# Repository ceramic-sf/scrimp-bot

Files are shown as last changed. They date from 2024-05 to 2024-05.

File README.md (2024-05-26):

# scrimp-bot
Make a bot from what you've got

movements

Tier|Bot|Reason
|-|-|-|
|S||
|A||
|B|scrimp bot | +Functional +Frugal -Fragile -Fortissimo -Flawed|
|C||
|F||

## Contents

  - [Goal](#goal)
  - [Free hardware](#free-hardware)
  - [Rationale](#rationale)
  - [Roller screw technology](#roller-screw-technology)
  - [Parts list](#parts-list)
  - [Simple form](#simple-form)
  - [Scrimp friendly](#scrimp-friendly)
  - [How control works](#how-control-works)
  - [How the muscle works](#how-the-muscle-works)
  - [Gearing](#gearing)
  - [Muscle module force](#muscle-module-force)
  - [Arm torque](#arm-torque)
  - [Telescopic design](#telescopic-design)
  - [Stepper and driver](#stepper-and-driver)
  - [Findings](#findings)
  - [Improvements](#improvements)
  - [Brains](#brains)

## Goal

For about 100 USD, build an arm that can lift regular objects around in a regular working space.

## Free hardware

Scrimpbot is free and open hardware, please enjoy.

open hardware

## Rationale

Robotic foundation models will soon make smooth control of rickety robots trivial.

One must have a robot to try them out. Scrimp bot is made from cheap parts a 3D printing hobbyist may already have
(filament, stepper motors, M3 bolts).

Words in -> vision-movement 2Hz looping -> smooth task completion

By mounting webcams on the robot, a script that takes images at 2Hz can feed the images containing
the robot position and environment to a model. The model puts out instructions to send to the robot. This implies that fine control will be possible, even if
the robot is not ultraprecise. Humans cannot do things precisely with their eyes closed, and neither can scrimp bot.

Scrimp bot is manually controllable with a few potentiometers. That allows
some training data to be made. A model fine tuned on those episodes can later
be used instead of the manual controller.

```mermaid
quadrantChart
    title Different Robots
    x-axis Basic Robot --> Complex Robot
    y-axis Basic Control --> Complex Control
    quadrant-1 Robust / SOTA / Future
    quadrant-2 Accessible and useful
    quadrant-3 Novelty
    quadrant-4 Manufacturing / Academia
    Octo + stepper: [0.1, 0.6]
    Octo + 3D printed arm: [0.25, 0.65]
    Optimus: [0.65, 0.75]
    Atlas: [0.85, 0.40]
    Spot: [0.60, 0.55]
    Arduino + 3D printed arm: [0.25, 0.25]
    Kuka: [0.55, 0.25]
```

## Roller screw technology

The main moving part in scrimpbot is the inverted planetary roller screw.

Its just a screw, but with low friction. That's good for robotics because
you don't want to lose any energy. Screws are nice because they can push heavy loads and you can tune them to make them stronger or faster.

If you want to explore this mechanism, consider printing this vise I designed and having a play. The roller screw there is the same that is used in scrimp bot.

[https://github.com/ceramic-sf/vice-vise/tree/main](https://github.com/ceramic-sf/vice-vise/tree/main)

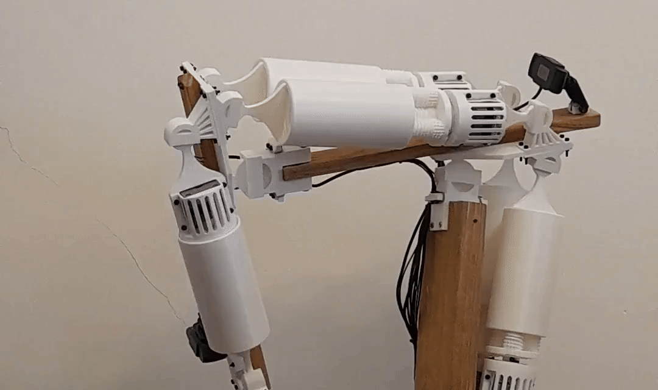
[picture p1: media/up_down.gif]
up_down


## Parts list

One may have most of these around the house.

| Item | Units | USD/unit | USD total | Mass/Unit (g) | Mass total (g) |
|---|---|---|---|---|---|
| PLA 1kg | 2 | 25 | 50 | 1000 | 2000 |
| NEMA 17 stepper motor | 5 | 5 | 25 | 300 | 1500 |
| M3 bolts/nuts 300pcs | 2 | 8 | 16 | 100 | 200 |
| Webcam 340p | 3 | 5 | 15 | 30 | 90 |
| TMC2208 drivers | 5 | 2 | 10 | 5 | 25 |
| Super glue tube | 3 | 2 | 6 | 1 | 3 |
| Wire 1m | 10 | 0.5 | 5 | 10 | 100 |
| Wood 2x4 1m | 1 | 5 | 5 | 1500 | 1500 |
| Variable resistors | 5 | 1 | 5 | 3 | 15 |
| Arduino | 1 | 5 | 5 | 25 | 25 |
| Power supply 24V 5A | 1 | 5 | 5 | 200 | 200 |
| Electrolytic Capacitor 100uF  | 1 | 1 | 1 | 1 | 1 |
| Rubber bands | 10 | 0.1 | 1 | 0.1 | 1 |
| **TOTALS** | | | **170** | | **5660** |

## Simple form

A mechanical muscle module that can lengthen and contract. Make multiple muscles to "flesh out" a robot skeleton.

The skeleton is wooden with some ball and socket joints.
Two muscles acting together can make a single joint roll, pitch and yaw. Multiple
joints allows for a large range of motion, similar to that of a human arm.

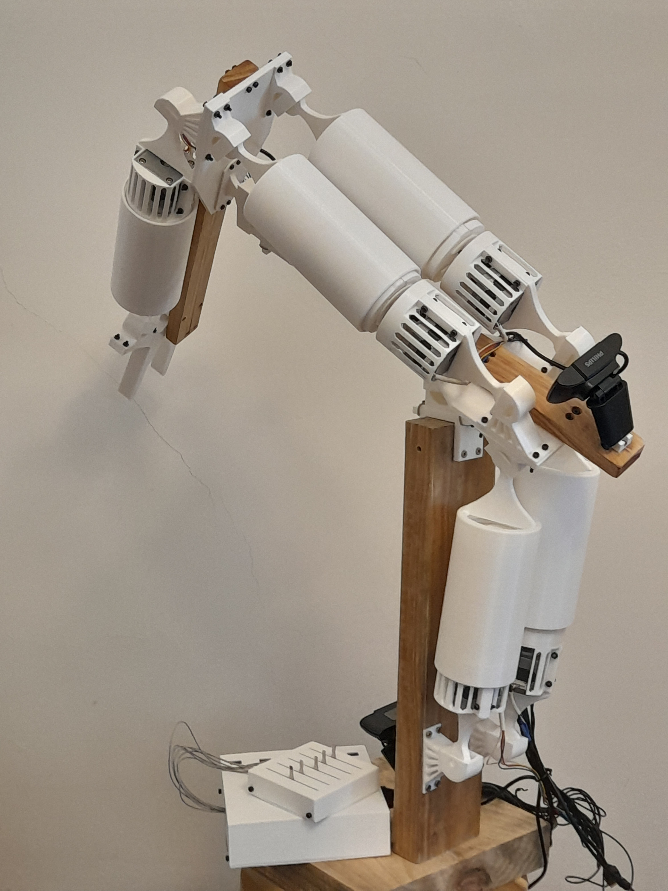
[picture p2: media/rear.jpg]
rear


## Scrimp friendly

The muscle module can fit any stepper size and length you have. The
FreeCAD model uses paramater based design and updating stepper sizes in the
CAD spreadsheet updates the physical model.

To use the FreeCAD model, open the `./models/muscle_motor_assembly.FCStd` file. The Assembly4 workbench is used to bring together different parts.

## How control works

Electronics go in a 3D printed box with some sliders that act as a remote control.

The human looks at the arm and moves the resistors, one per muscle.
Each resistor is read by the arduino and converts position into a velocity.
The signal is sent to the stepper driver, which sends signals to the stepper. The stepper spins
the roller screw, which changes the muscle length. The arm moves. One muscle operates a crab claw.

Theoretically, the control box can be removed and the webcams turned on. Then
one would type instructions on a laptop, and a robot foundation model would move scrimbot

## How the muscle works

Stepper motors are high torque with low speed. A 34mm NEMA17 can get about 3 rotations per second
(180RPM). If applied to a screw system with a lead of 5-15mm/rotation that can result in a linear movement of
15-45mm/sec. This linear movement is the same as the linear movement of a contractile muscle, simply fix it to a bone either side of a joint.

## Gearing

A roller screw is useful in transmitting work efficiently (80-90%). The screw can be designed
to have higher speed or higher torque. This allows the mechanical advantage to be tuned
easily.

For a better understanding of how this works, try out this
[roller screw recipe](https://github.com/ceramic-sf/vice-vise/blob/main/roller_screw_recipe.md).

Additionally, the where the muscle is attached and how long the limb is can be modified
for higher speed or higher torque.

## Muscle module force

The stepper motor performs work during a full revolution. That work
is equal to the work done by the muscle module which exterts a constant force
over the lead of the roller screw.

Let's calculate the force. We know what torque the stepper exerts (datasheet). We
know that the force exterted will be different if the lead is high (low torque) or
low (high torque).

Mechanically this is the same as a rack (screw) and pinion (stepper). The pinion
gear turns one revolution and the rack moves one lead distance. So the pinion circumference is equal to the screw lead. That lets us calculate the radius of the
pinion, which is where the force is being exterted on the rack.
```
stepper_torque_nm = force_exterted_n * pinion_radius_meters
force_exerted_n = stepper_torque_nm / pinion_radius_meters
```
Where:
```
circumference_pinion_meters = roller_screw_lead_meters
```
Replace circumference with radius and rearrange:
```
pinion_radius_meters = roller_screw_lead_meters / 2 * pi
```
So, the newtown force for a given newton meter torque input of a stepper motor
driven roller screw is:
```
force_exerted_n = 2 * pi * stepper_torque_nm / roller_screw_lead_meters
```

Leads are usually in millimeters and stepper datasheets often have kgcm torque. Where:
```
stepper_torque_nm = stepper_torque_kgcm * g_gravity / 100
```
The useful formula is:

```
force_exerted_n = 20 * pi * g_gravity * stepper_torque_kgcm / roller_screw_lead_millieters
```
Simplified:
```
force_exerted_n ~= 630 * stepper_torque_kgcm  / roller_screw_lead_millimeters
```
However, transmission of a roller screw is not perfect (80-90% efficient).
Using 80% efficiency:
```
force_exerted_real_n = 500 * stepper_torque_kgcm / roller_screw_lead_millimeters
```
Which for a cheap step stepper with 1.3kgcm torque and a lead of 10mm results
in a torque of ~65N.

## Arm torque

The stepper motor has torque that drives the screw, which exterts a constant push or pull force. That force is applied on the moving bone of a skeleton, some distance from the joint.

We can attach the muscle module to work as a first-class (seesaw, tricep muscle) or a second-class  (wheelbarrow, bicep muscle) lever. A first class keeps the
muscles more out of the way.

So the muscle attaches on one side of the joint (`attached_distance_m`) and
moves the arm (`arm_length_m`).

The largest mass that can be lifted by an arm with a single muscle motor module can be calculated. Let the muscle torque and the lifting torque be equal:

```
muscle_module_force * attached_distance_m = kg_liftable * g_gravity * arm_length_m
```
So max `kg_liftable`:
```
kg_liftable = muscle_module_force * attached_distance_m / (g_gravity * arm_length_m)
```

We now use the muscle module force calculation from before:
```
kg_liftable = 50 * stepper_torque_kgcm * attached_distance_m / (arm_length_m * roller_screw_lead_millimeters)
```

So if we use a standard NEMA17, a 10mm lead, connect the muscle 10cm from the joint and have the arm be 40cm long then the liftable mass is 1.6kg.

The actual prototype has a 4mm lead, muscle connected at 10cm, and a 30cm arm. So the liftable mass is 5.4kg. Two muscles are used, which gives ~10kg liftable mass in theory. Some of that mass will be lifting the outer parts of the arm (wrist and claw motors and parts).

## Telescopic design

In this design, the stepper motor is integrated with the inverted planetary roller screw to form a plug and play
motor muscle module.

The main features of this design are:
- The stepper motor is protected from axial loads via a printed slew bearing
- The stepper motor telescopes into the nut of the roller screw which reduces the length of the
muscle module.

An inverted planetary roller screw facilitates the teslescope action, where a non-inverted
would not.

## Stepper and driver

Old discarded NEMA17 steppers:
- Model: KH42HM2B017
- Coil: 30ohms/phase
- Current: 0.82A/phase
- Rated holding torque: 1.3kgcm
- Axial housing length: 34mm

Driver:
- Model: TMC2208 (the stepper is nearly silent with this driver)
- Mode: Half step (reduces torque, but full step requires sending driver signals in a more complicated way)
- Current limit: 0.54A
    - `reference_voltage = max_current * 1.41 = 1.0V`
    - Initially 0.8A was used (stepper datasheet), but was too hot.

See [scrimp_bot_wiring.md](./scrimp_bot_wiring.md) for a wiring diagram of all connections for electronics.

## Findings

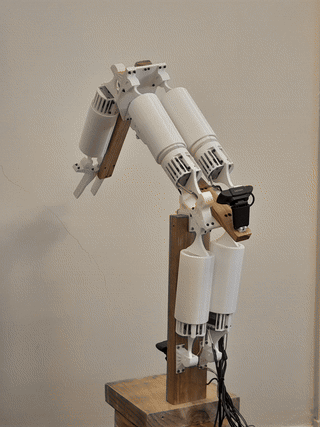
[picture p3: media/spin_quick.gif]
spin


It works, but some mods are in order.

| Feature | Problem | Suggestion |
|---|---|---|
|Muscle modules|Large diameter means they rub|Stop telescoping stepper into nut.|
| Stepper Motor Telescoping | Stepper motor makes the nut large and modules rub | Place stepper next to nut and drive the nut |
| Stepper Motor Telescoping | Roller screw cannot be sealed for noise and lubrication | Keep stepper out of nut, seal mechanism |
| Thread Starts | One thread start makes the screw structurally vulnerable. | Use 2 or 3 thread starts to improve structural integrity. |
| Motors always on | Motors reach around 70 degrees, causing PLA to glass. | Turn off current when not moving. |
| Bearings | Bearings add friction and may be unnecessary as PLA would break first. | Remove bearings and let stepper take axial load. |
| Stepper Motor Installation | Stepper motor is fiddly to install. | Use a face plate for easier installation and removal. |
| Stepper Motor Shaft | No grip for the grub screw. | Grind the shaft to a "D" shape for better grub screw grip. |
| Lift Capacity and Speed | Lift capacity is good, but movement is slow. | Use longer stepper motors and higher lead roller screws. |
| Ball and Socket Joints | Joints work well but had a dislocation. | Reinforce socket or redesign joints. |
| Tendon-Based Attachments | Tendon-based attachments need supports to print | Separate tendons fromo joints |
| Stepper Motor Enclosure | Enclosure obstructs heat dissipation, potentially causing PLA to melt. | Design the enclosure to improve heat dissipation. |
| Noise Level | Mechanism is moderately noisy. | Seal and lubricate the mechanism to reduce noise. |

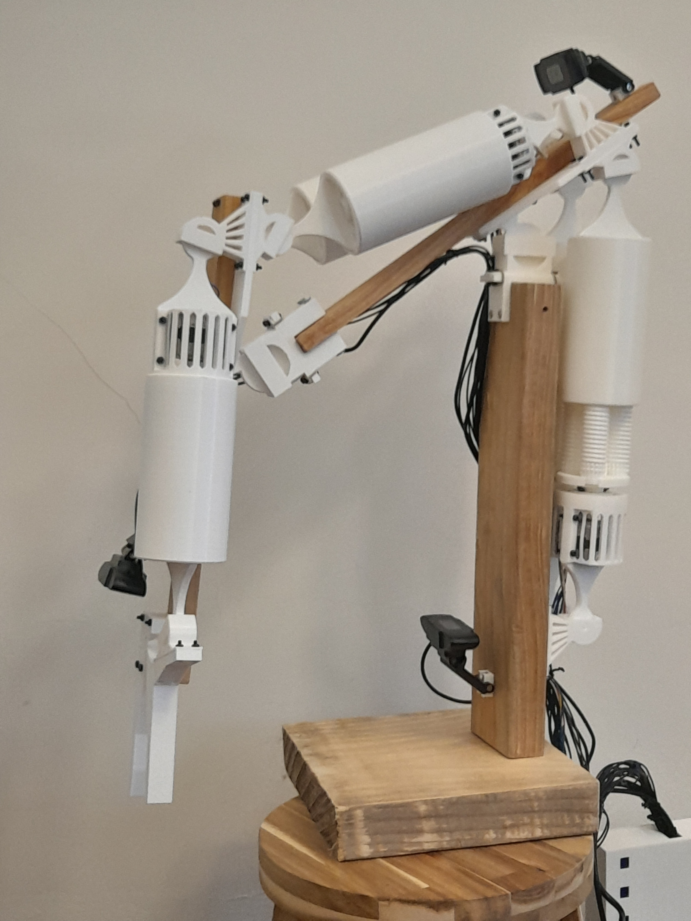
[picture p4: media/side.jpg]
side


## Improvements

A next iteration of scrimp bot given the above findings Given the above direction is:
- Reduce complexity
- Remove features

New design:
- Stepper bolted to a hinge
- Stepper shaft bolted to end of nut
- Muscle motor modules will have smaller radius
- Roller screw mechanism stays inside nut
- A cental screw extension rod is bolted to a joint

## Brains

Scrimpbot can theoretically be driven by a robotic foundation model.

See [scrimp bot brains](./scrimp_bot_brains.md) for a work-in-progress walkthrough of the most straightforward path I can see being feasible.

The hardware roughly looks like this:
```mermaid
---
title: Hardware arrangement
---
flowchart LR
    subgraph computer[server]
        octo[octo weights]
        subgraph scripts[python scripts]
            photo[take photos] --> inference
            inference[run octo inference] --> command
            command[send motor commands]
        end
        camera[webcam]
    end

    subgraph robot
        driver[stepper driver]
        command --> driver
        power[power supply] --> capacitor
        capacitor --> driver
        driver --> motor
    end
```

The software mainly does this:
```mermaid
---
title: Cycle repeated every n milliseconds
---
flowchart TD
    camera[camera takes photo of robot] --> inference[octo inference run on photo to get rotation commands]
    inference --> commands[rotation step commands to driver]
    commands --> driver[driver converts steps to electric pulses] --> motor[motor moves to some new position]
    motor --> camera
```

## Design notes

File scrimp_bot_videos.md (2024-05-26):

Scrimp bot is noisy, see [./media/raw_with_audio.mp4](./media/raw_with_audio.mp4)
for a sample with audio. The roller screws are open and resonate inside the large PLA nut cylinder.

When you extend a muscle too far, nothing stops it from falling apart.

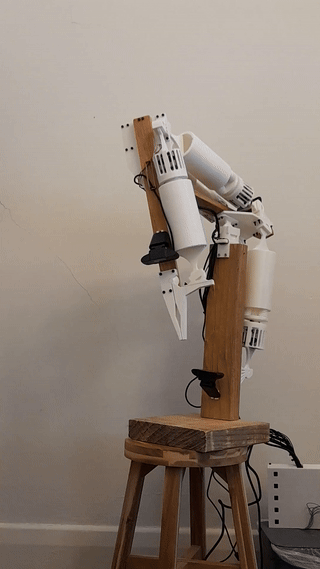
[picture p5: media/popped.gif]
popped


Demo of how the joints tilt.

side_to_side

Range low down.

sweep

Preparing the claw to grab something.

go_to_grab

Scrimp bot is hard to get where you want exactly.

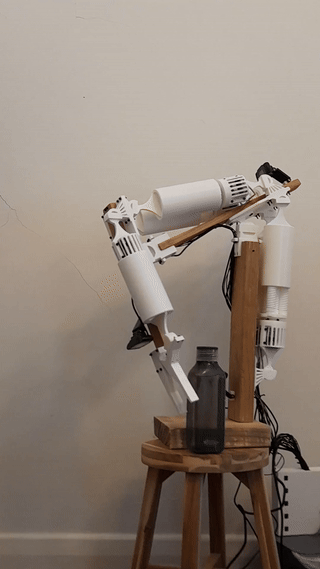
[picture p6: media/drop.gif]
drop


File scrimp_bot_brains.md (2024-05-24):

# scrimp bot box

How to use Engligh sentences to control a home made robot.

"Grab to the banana"

Status: Ideas/research phase.

Progress: Search for the "🚧 progress marker 🚧" below.

## Introduction

An exploration of the Octo robot control model ([https://github.com/octo-models/octo](https://github.com/octo-models/octo)) running on a dedicated box connected to a cheap
homemade robot.

Octo uses images of the robot to work out what the robot should do. Cheap webcams are attached
to the robot, the cameras can see part of the robot and part of the environment.
Cameras are the only positional feedback that the robot has.

## Server setup

An i5 without is used without a dedicated GPU. Webcams and arduino are
plugged in over USB.

- Download ubuntu, burn to usb, install on pc, configure, SSH in from laptop

## Robot hardware setup

Build a robot that can be controlled by an arduino.

- Construct parts, add motors, connect drivers to motors, connect arduino to drivers.

## Robot software setup

Create a python script that can send data to the arduino via serial interface.

## Using octo to move the robot

Scrimp bot is a single stepper motor in front of a camera that can point
to objects drawn on a clockface. It is controlled by text input to a vision-enabled transformer that outputs
rotation commands.

scrimp bot is interesting because you can keep adding motors and
sensors and make incremental progress to more accessible and useful
robotics.

```mermaid
quadrantChart
    title Different Robots
    x-axis Basic Robot --> Complex Robot
    y-axis Basic Control --> Complex Control
    quadrant-1 Robust / SOTA / Future
    quadrant-2 Accessible and useful
    quadrant-3 Novelty
    quadrant-4 Manufacturing / Academia
    Octo + stepper: [0.1, 0.6]
    Octo + 3D printed arm: [0.25, 0.65]
    Optimus: [0.65, 0.75]
    Atlas: [0.85, 0.40]
    Spot: [0.60, 0.55]
    Arduino + 3D printed arm: [0.25, 0.25]
    Kuka: [0.55, 0.25]
```
Octo accepts language commands and sensor input and outputs commands for a robot controller to follow.

This is interesting because you can give a complicated command like "point to the cat"
and the model will watch as progress unfolds and update commands on the fly.

One can imagine a robot with only cameras for sensors and direct motor control. This walkthrough
attempts that with a single stepper motor with a camera pointed at it. The motor can rotate to
point at different pictures. An instruction "point to the cat" can be given, the model
is regularly fed camera frames of the motor, the model outputs rotation commands, and the commands
are sent by a microcontroller to the motor.

First we will try with the model as it is published, which would be an environment the model
has never seen and may not work well. Then we can fine tune the model by recording episodes
manually and then storing them in a particular format and fine tuning the model.

If the basic test works, it will be easy to add more motors and cameras. At that point we would
have a robot arm that only relies on sight for control, and it would be good to see if complex and
precise tasks could be performed. From there, one could make a two handed robot and see if that
works. Sensors can also be added as inputs. At this point, one could have a low cost
robot arm setup that can respond to human language.

### Observations
We can see that the model will accept a primary image and/or a wrist image.
We have only passed a primary image (supposed to be a main image of the robot,
but we used a dummy image).

These are all things that we can redefine when fine tuning the model later.
So a robot may have 3 images from different angles, and no wrist image. Or
it may have only one image and several force sensors.
```console
Observations: {
    image_primary: ('batch', 'history_window', 256, 256, 3),
    image_wrist: ('batch', 'history_window', 128, 128, 3),
}
```
### Tasks
We sent a text task, but we could have also sent a target image. That
is, an ideal end point that the robot should look like once it is finished,
either from zoomed out, or from the wrist perspective.
```console
Tasks: {
    image_primary: ('batch', 256, 256, 3),
    image_wrist: ('batch', 128, 128, 3),
    language_instruction: {
        attention_mask: ('batch', 16),
        input_ids: ('batch', 16),
    },
}
```
### Actions
Then we see actions the model thinks are appropriate.

The model produces 7 actions, 4 steps into the future. We can that there are
4 sets of seven action values in the output:
```console

'pick up the fork' actions:
[[[ 0.69299155  0.19062363 -0.05662455  0.18763681  0.07296022
   -0.3521931   1.0031093 ]
  [ 0.9940647   0.23903748 -0.11212341  0.32031953 -0.00594463
   -0.4033823   0.9950697 ]
  [ 1.130245    0.18083405 -0.37783027 -0.36048374  0.25762615
   -0.5909108   0.9917318 ]
  [ 0.7212891  -0.0667934  -0.48938182 -0.23768651 -0.03046823
    0.13813896  0.9990556 ]]]

'push the apple' actions:
[[[ 0.88822544  0.03327435 -0.01053857  0.11183605  0.22582716
   -0.25007552  1.0030512 ]
  [ 1.2086031   0.0545348  -0.17068534  0.21365923  0.18337864
   -0.3036416   1.0020596 ]
  [ 1.2331996  -0.00789991 -0.5044224  -0.3035693   0.39421743
   -0.44048995  0.9858144 ]
  [ 0.838152   -0.22254696 -0.6525285  -0.26379094 -0.10052849
    0.11552006  1.0055982 ]]]
```
So the model thinks that the first thing we should instruct the
robot to do to pick up the fork is:
```json
[ 0.69299155  0.19062363 -0.05662455  0.18763681  0.07296022 -0.3521931   1.0031093 ]
```
What do these values mean? Each robot will have different ways to control it.
So `0.692` could mean:
- Move motor one `0.69` meters
- Move motor two `69%` of a full rotation
- Close gripper until `0.69N` of force is archieved.
- ...

We will need to think about what actions are appropriate for our robot,
then define them in the model. The model will then be able to output
actions that can be used. If the robot is different from anything it has
seen, or the robot control problem is very difficult, then fine tuning
on examples will be required to allow the model to learn. After
learning, the model will be better at selecting actions that achieve
the tasks better.

## Looping

Take photo, run model, send action to robot, repeat.

A single inference took 0.18s to run on a quad core i7. This implies
that you could complete 5 send command, receive image cycles per second.

## Changing the model output

Octo accepts two images (primary, wrist) and outputs seven values.

```mermaid
---
title: Off the shelf Octo configuration
---
flowchart TD
    subgraph observations
        primary[primary image]
        wrist[wrist image]
    end
    observations --> octo --> actions
    subgraph actions
        floats[7 numbers]
    end
```
Additionally, the model is configured to use previous images and predict future
actions as follows
- `history_window`. How many previous inputs to use, default is 2.
- `action_chunking`. How many actions to predict, default is 4.

```mermaid
---
title: historical window size and action chunking
---
flowchart TD
    subgraph history[history windows, `window_size=2`]
        obs_m_1[observation m - 1]
        obs_m[observation m]
    end

    octo
    obs_m_1 & obs_m --> octo

    subgraph action[action chunking, 'pred_horizon=4']

        act_n[action n]
        act_n_1[action n + 1]
        act_n_2[action n + 2]
        act_n_3[action n + 3]
    end
    octo --> act_n & act_n_1 & act_n_2 & act_n_3
```

The model is defined here `./octo-small/config.json`, and the key parts
of the config are:
- `model`
    - `observation_tokenizers`
        - `primary` (image)
        - `wrist` (image)
    - `task_tokenizers` (text input)
    - `heads`
        - `action`
            - `action_dim` (size of each model action)
            - `pred_horizon` (number of actions to output per inference)
    - `window_size` (number of historical positions to use)

### Understanding model modifications
The octo repo example `./octo/examples/02_finetune_new_observation_action.py` shows how to modify the model to be used in the Aloha dataset. This is a bimanual robot.
We will use that to learn how changing the observations and actions of
a model works.

```mermaid
---
title: (Example 2) Aloha fine tuning example Octo configuration
---
flowchart TD
    subgraph observations
        primary[primary image]
        proprioception[14 proprioception numbers]
    end
    observations --> octo --> actions
    subgraph actions
    floats[14 numbers]
    end
```
Interestingly, the Aloha example does not use multiple historical windows.
```mermaid
---
title: (Example 2) Aloha historical window size and action chunking
---
flowchart TD
    subgraph history[history windows, `window_size=1`]
        obs_m[observation m]
    end

    octo
    obs_m --> octo

    subgraph action[action chunking, 'pred_horizon=50']

        act_n[action n]
        act_n_1[action n + 1]
        act_n_2[action ...]
        act_n_3[action n + 49]
    end
    octo --> act_n & act_n_1 & act_n_2 & act_n_3
```

First, the `./octo-small/config.json` config is read. Then it is modified
to suit the Aloha dataset.

```python
# `./octo/examples/02_finetune_new_observation_action.py`
def main(_):
    # ... (omitted)
    # Load octo-small config
    pretrained_model = OctoModel.load_pretrained(FLAGS.pretrained_path)
    # Load new dataset
    logging.info("Loading finetuning dataset...")
    dataset = make_single_dataset(
        dataset_kwargs=dict(
            name="aloha_sim_cube_scripted_dataset",
            data_dir=FLAGS.data_dir,
            # One input image.
            # This is a helper as images are labelled "top", not "primary"
            image_obs_keys={"primary": "top"},
            # In the dataset, proprioception is called "state" and has 14 elements.
            state_obs_keys=["state"],
            language_key="language_instruction",
            action_proprio_normalization_type=NormalizationType.NORMAL,
            # An action contains 14 values.
            absolute_action_mask=[True] * 14,
        ),
        traj_transform_kwargs=dict(
            # No historical windows.
            window_size=1,
            # Produces the next 50 actions every inference (action chunking).
            future_action_window_size=49,
        ),
        frame_transform_kwargs=dict(
            resize_size={"primary": (256, 256)},
        ),
        train=True,
    )
    # ... (omitted)

    config = pretrained_model.config
    ### The wrist camera observation is not needed for Aloha.
    del config["model"]["observation_tokenizers"]["wrist"]

    ### Add new observation for proprioception ()
    config["model"]["observation_tokenizers"]["proprio"] = ModuleSpec.create(
        LowdimObsTokenizer,
        n_bins=256,
        bin_type="normal",
        low=-2.0,
        high=2.0,
        obs_keys=["proprio"],
    )
    # Fully override the old action head with a new one (for smaller changes, you can use update_module_config)
    config["model"]["heads"]["action"] = ModuleSpec.create(
        L1ActionHead,
        pred_horizon=50,
        action_dim=14,
        readout_key="readout_action",
    )
```
We can use this code to understand how to change the model to suit a new robot.

### Define the scrimp bot model

We would like to make it accept one image (camera view of the motor) and output two values (a rotation command to motor and a "finished" signal). We will keep the window size and prediction horizon as the default values until there is a good reason to change them.

```mermaid
---
title: Desired basic Octo configuration
---
flowchart TD
    subgraph observations
        primary[primary image]
    end
    observations --> octo --> actions
    subgraph actions
    floats[2 numbers]
    end
```
So, we could follow a similar procedure for a new model definition and dataset.
We can do that later. We will first test the unaltered model to understand the
control system.

## Hardware

For using the octo model to control the robot:

- Server
    - Intel i5
    - 16Gb RAM
    - 100GB drive
- MicroSD with >4GB
- 3x cheap USB webcams
- Stepper motor driver (e.g., A4988 or TMC2208)
    - More info see here https://howtomechatronics.com/tutorials/arduino/stepper-motors-and-arduino-the-ultimate-guide/
- NEMA17 stepper motors
- 24V AC to DC converter rated to 1A or more
- 100uF electrolytic capacitor

```mermaid
---
title: Hardware arrangement
---
flowchart LR
    subgraph computer[server]
        octo[octo weights]
        subgraph scripts[python scripts]
            photo[take photos] --> inference
            inference[run octo inference] --> command
            command[send motor commands]
        end
        camera[webcam]
    end

    subgraph robot
        driver[stepper driver]
        command --> driver
        power[power supply] --> capacitor
        capacitor --> driver
        driver --> motor
    end
```

```mermaid
---
title: Cycle repeated every n milliseconds
---
flowchart TD
    camera[camera takes photo of robot] --> inference[octo inference run on photo to get rotation commands]
    inference --> commands[rotation step commands to driver]
    commands --> driver[driver converts steps to electric pulses] --> motor[motor moves to some new position]
    motor --> camera
```

### Later: Hardware for fine tuning

For fine tuning the octo model

- Server and robot setup from before
- Manual control system to move the robot.
    - For a single-motor robot, a resistor pot and a script to control stepper motor velocity
    is enough
    - Keyboard input mapped to each joint
    - For a complex robot, a miniature robot rigged with resistor pots can be used to control the
    large one naturally
    - Joystick configured to control end effector movements
- GPU
    - NVIDIA GPU with at least ~1GB VRAM
- Time to perform robot movements manually and record data for ~50 episodes "things you want the
robot to do"
- Time to run fine tuning

## Set up dedicated server

Flash the SD card with ubuntu server.
SSH in.

```
ssh scrimpbot@<serveripaddress>
sudo apt update && sudo apt full-upgrade
sudo apt install -y python3-pip make build-essential libssl-dev zlib1g-dev \
libbz2-dev libreadline-dev libsqlite3-dev wget curl llvm libncurses5-dev \
libncursesw5-dev xz-utils tk-dev libffi-dev liblzma-dev git-lfs
```
Install pyenv as per https://github.com/pyenv/pyenv

Make an environment
```
mkdir scrimpbot && cd scrimpbot
pyenv install 3.10
pyenv virtualenv 3.10 scrimpbot-venv
pyenv activate scrimpbot-venv
```

Get octo and install octo as a python package
```
git clone https://github.com/octo-models/octo.git
```
In `requirements.txt`, make sure that scipy is `scipy>1.6.0,<=1.12.0` (see https://github.com/octo-models/octo/issues/71).
```
pip install -e octo
pip install -r octo/requirements.txt
pip install --upgrade "jax[cpu]==0.4.20" jaxlib
```

Download the small octo model (27M params)
```
git clone https://huggingface.co/rail-berkeley/octo-small
```
See that the ~500MB of weights are installed (requires git lfs)
```
du -sh octo-small/270000
> 522M	octo-small/270000
```
Create a test script
```
cd /home/scrimpbot/scripts
nano basic_inference_test.py
```
Containing:

```py
import jax
from octo.model.octo_model import OctoModel
import matplotlib.pyplot as plt
import numpy as np
from PIL import Image

def run():
    # The model accepts an image of a robot.
    # Lets use the welcome image for octo.
    # (x, y, rgb)
    img = np.array(Image.open("./octo/docs/assets/teaser.jpg").resize((256, 256)))

    # Add dimensions for batch number and time sequence.
    # (batch, time, x, y, rgb)
    img = img[np.newaxis,np.newaxis,...]
    # Load the weights (~550MB)
    model = OctoModel.load_pretrained ("./octo-small")
    # Print info about what the model accepts.
    print(model. get_pretty_spec ())

    # We will send the image as a "primary image" to the model (not a wrist image).
    observation = {"image_primary": img, "pad_mask": np.array([[True]])}
    # Define the task as a language task (rather than an image target task)
    task = model.create_tasks (texts =["pick up the fork"])
    # Actions will be based on observations and tasks.
    # A random seed can be used for reproducible outputs.
    action = model.sample_actions (observation, task, rng=jax.random.PRNGKey (0))
    # [batch, action_chunk, action_dim]
    print(f"'pick up the fork' actions: \n{action}\n")
    # Test a second task on the same image:
    task = model.create_tasks (texts =["point to the apple"])
    action = model.sample_actions (observation , task , rng=jax.random.PRNGKey (0))
    print(f"'push the apple' actions: \n{action}\n")

if __name__=="__main__":
    run()
```
Run it
```command
python basic_inference_test.py
```
The script prints out information about the model (observations and actions) and then the model output (actions)
that are derived from the input image (dummy image).

## Set up camera script

Next we set up the camera that will be taking frequent photos of the robot. These photos will
be passed to the model at about 2Hz.

Connect the camera to the server via USB. The camera here is a cheap fixed focal length webcam
with 720p resolution.
```
lsusb
```
Allow the user to use video devices:
```
sudo usermod -a -G video $USER
```

We already have `imageio` installed courtesy of octo.

Make a script `./scripts/take_photo.py`. Make a photo directory `./photos/`
```py
import imageio

def capture_image_with_imageio():
    # Create a reader object for the camera
    reader = imageio.get_reader('<video0>')  # Adjust the device index as needed

    # Get the first frame from the video
    image = reader.get_next_data()

    # Save the image
    imageio.imwrite('./photos/photo.jpg', image)

    # Close the reader
    reader.close()
    print("Image captured and saved.")

capture_image_with_imageio()
```
Run the script:
```
python scripts/take_photo.py
```
On host terminal, fetch and look at the photo to make capture works.
```
scp username@server_ip:/path/to/image.jpg .
open image.jpg
```

## Inference from live photos

Now we connect the camera feed to octo.

Make a new script `./scripts/live_camera_test_inference.py`

```py
import imageio
import jax
from octo.model.octo_model import OctoModel
import matplotlib.pyplot as plt
import numpy as np
from PIL import Image

def run():
    # Load the weights (~550MB)
    model = OctoModel.load_pretrained ("./octo-small")
    # Print info about what the model accepts.
    print(model. get_pretty_spec ())

    # Create a reader object for the camera
    reader = imageio.get_reader('<video0>')

    for i in range(10):
        image_frame = reader.get_next_data()
        img_pil = Image.fromarray(image_frame)
        img = np.array(img_pil.resize((256, 256)))

        # Add dimensions for batch number and time sequence.
        # (batch, time, x, y, rgb)
        img = img[np.newaxis,np.newaxis,...]

        # We will send the image as a "primary image" to the model (not a wrist image).
        observation = {"image_primary": img, "pad_mask": np.array([[True]])}
        # Define the task as a language task (rather than an image target task)
        task = model.create_tasks (texts =["pick up the fork"])
        # Actions will be based on observations and tasks.
        # A random seed can be used for reproducible outputs.
        action = model.sample_actions (observation, task, rng=jax.random.PRNGKey (0))
        print(f"Image {i} action: \n{action}\n")
    reader.close()

if __name__=="__main__":
    run()
```

This produces a series of outputs:

```
Image 0 action:
[[[ 1.0211147   1.3322583   3.5193803   1.5733439   0.77802694
    0.14373209  1.0019149 ]
  [ 1.8611907   1.6791227   2.7808633   2.3033714   2.293345
    0.07691714  0.98992133]
  [ 1.7638344   0.71729124  0.60360736 -0.8126997   2.7541971
   -0.73859084  1.0238383 ]
  [ 0.04364672 -0.01568194 -0.07068803  0.00706088  0.02779285
    0.03208306  1.0020238 ]]]

...

Image 9 action:
[[[-0.26176193  0.4993779   3.334176    0.49208674  0.43199566
   -0.15955538  1.006547  ]
  [ 0.05474208  0.77473545  2.7656777   1.4154626   1.3524969
   -0.26994956  0.9889633 ]
  [ 0.02293671  0.00509753 -0.06992306 -0.05930427  0.19169654
   -0.08868875  1.0153261 ]
  [-0.00515349  0.03184005 -0.00537145 -0.04313584  0.03046033
    0.01828552  0.994661  ]]]
```

Loading the model takes about 15s.

For each image capture and infer loop, the model takes about 0.3s. This fast enough for now
and is just using the CPU.

## Set up communication from server to arduino

An arduino will be used to send messages to the stepper motor driver. The arduino will receive
commands over USB from the server. We will test this setup using dummy values from
the server to control flashes of the built in LED on the arduino.

Connect the arduino to the laptop and use the arduino IDE to flash the following script to it:
```arduino
const int ledPin = 13; // LED connected to digital pin 13

void setup() {
  pinMode(ledPin, OUTPUT);
  Serial.begin(9600);
}

void loop() {
  if (Serial.available()) {
    String data = Serial.readStringUntil('\n'); // Read the incoming data until newline
    int lastPos = 0;
    int pos = 0;
    while ((pos = data.indexOf(',', lastPos)) != -1) {
      String value = data.substring(lastPos, pos); // Extract each command
      lastPos = pos + 1;
      executeFlash(value.toFloat());
    }
    executeFlash(data.substring(lastPos).toFloat()); // Execute the last command
  }
}

void executeFlash(float duration) {
  int flashes = duration == 0.2 ? 2 : 3;
  for (int i = 0; i < flashes; i++) {
    digitalWrite(ledPin, HIGH);
    delay(500);
    digitalWrite(ledPin, LOW);
    delay(500);
  }
  delay(1000); // Wait after the sequence
}
```

Unplug the arduino and plug it into the server via USB. Immeditately look at diagnostic
messages to see the device name.

```
dmesg | tail
```
Look for the name. In this case `ttyACM0`
```
> ttyACM0: USB ACM device`
```
Look at the permissions for the device:
```
ls -l /dev/ttyACM0
> crw-rw---- 1 root dialout ... /dev/ttyACM0
```
The device belongs to the `dialout` group and so if we add our user to that group, it will have
access to the serial port.
```
sudo usermod -a -G dialout $USER
```
Restart the shell to action the change.
```
exec "$SHELL"
```

On the server install `pyserial`
```
pip install pyserial
```
Make a new script: `./scripts/send_test_arduino_command.py`

```py
import serial
import time

# Set up serial connection (adjust the port name as per your system, e.g., /dev/ttyUSB0 or /dev/ttyACM0)
ser = serial.Serial('/dev/ttyACM0', 9600, timeout=1)
time.sleep(2)  # Wait for the connection to be established

# Hardcoded array of values to send to the Arduino, sent as a single concatenated string
values = [0.2, 0.3, 0.3, 0.2, 0.2, 0.3, 0.3, 0.2, 0.3, 0.3]
message = ','.join(str(v) for v in values) + '\n'  # Join all values with commas and add newline

try:
    ser.write(message.encode())  # Send the entire message at once
    print("Sent:", message)
    time.sleep(10)  # Give Arduino time to process all commands

except KeyboardInterrupt:
    print("Program exited.")

finally:
    ser.close()  # Always close the serial connection when done
```
Run the script
```
python scripts/send_test_arduino_command.py
```
This prints a sequence and the arduino should blink to the same pattern.
```
Sent: 0.2
Sent: 0.3
...
Sent: 0.3
Sent: 0.3
```

## Make the script to modify the model output to suit a single motor

At present the octo model produces seven values. We will change that to
one value because we only want to control a single motor for the first
test. There are two parts to this: modify the config used and create a new data set.

When we looked at `./octo/examples/02_finetune_new_observation_action.py` earlier,
we saw how we can load the `./octo-small/config.json` config file and then
modify parts of it. Instead of fine tuning for the aloha dataset as shown in the
example we will change it to use a single camera view to control a single motor.

We will actually add another element to the model output, to declare when
the model believes it is finished. This will be a binary output (0 still going,
1 finished).

Here is a summary `./octo-small/config.json`, and the changes we will make
inside the python program (we will not modify `config.json` directly).

- `model`
    - `observation_tokenizers`
        - `primary` (image)
        - `wrist` (image - remove)
    - `task_tokenizers` (text input)
    - `heads`
        - `action`
            - `action_dim` (size of each model action. Change to 2)
            - `pred_horizon` (number of actions to output per inference. Change to 1.)
    - `window_size` (number of historical positions to use. Change to 1.)

---------
---------
🚧 progress marker 🚧
---------
---------

Make a new file `./scripts/fine_tune_single_stepper.py`

```python
TODO
```

This script will use a new dataset to modify the octo model.

## Make a new dataset

We will fine tune the octo model with a custom dataset.
This is how octo will know the particulars of out robot.

The dataset must be provided in RLDS format.

The main idea is to create a dataset of episodes where the robot
completes some task. The episodes can be anything, but must be recorded
in RLDS format (https://github.com/google-research/rlds and https://github.com/kpertsch/rlds_dataset_builder).

## Run fine tuning using the new dataset

```command
python fine_tune_single_stepper.py --pretrained_path=./octo-small --data_dir=...
```

## Make the arduino receive model outputs

todo

## Set up the motor

The model will output a velocity for the motor. The arduino will convert this
velocity into steps and direction, which will then be sent to the stepper motor
driver periodically. The driver will then send pulses to the motor, which
will move.

## Integrate octo and the camera and stepper

Write a script that will take a photo, pass it to octo, parse the
result as a rotation command for the stepper, then send the command
to the stepper driver. Then repeat after a delay, and stop at some point.

```py
# TODO ./scrimpbot/deploy.py
```

## Repeat the single stepper procedure, but with scrimp bot

## Give scrimp bot a banana

Type in "grab the banana", and see if scrimp bot can do it.

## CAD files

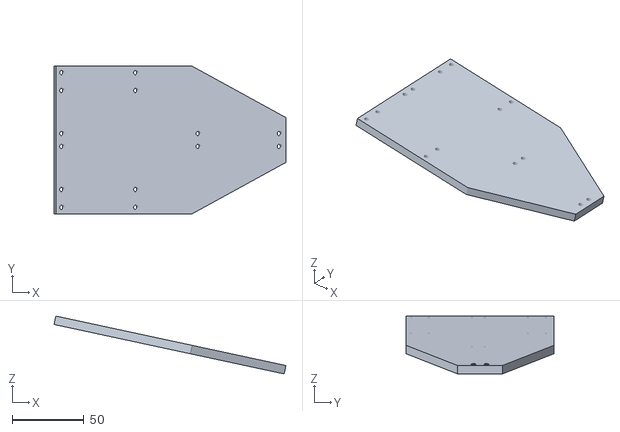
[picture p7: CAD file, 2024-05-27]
models/stl/swivel_plate.stl
162.0 x 103.1 x 40.4

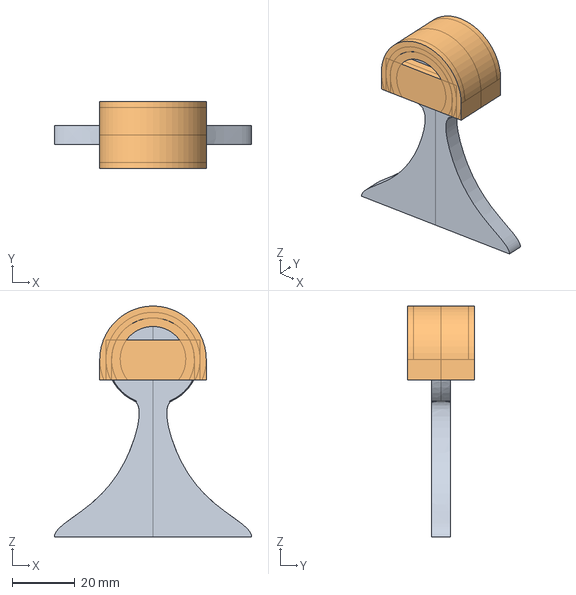
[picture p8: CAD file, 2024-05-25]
models/tendon.FCStd
63.0 x 21.5 x 73.7 mm
tendon_body
enthesis_body

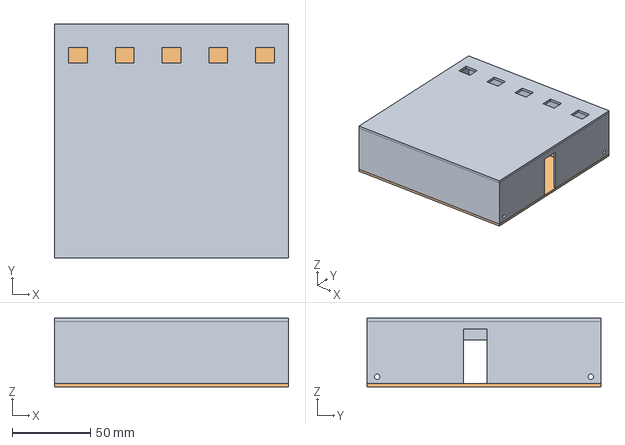
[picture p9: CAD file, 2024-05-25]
models/driver_box.FCStd
150.0 x 150.0 x 44.0 mm
driver_body
cover_body

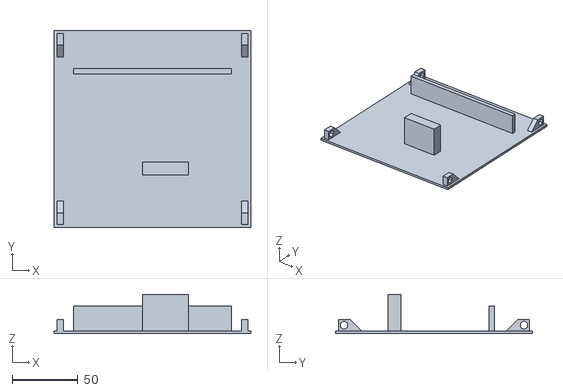
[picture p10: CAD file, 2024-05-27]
models/stl/driver_box_top.stl
150.0 x 150.0 x 30.0

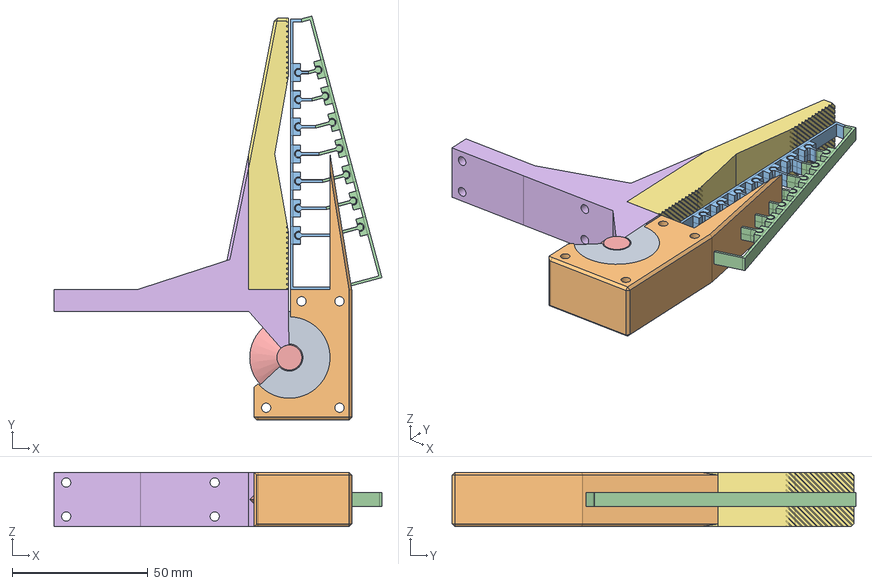
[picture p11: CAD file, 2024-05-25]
models/gripper.FCStd
120.8 x 148.8 x 20.0 mm
static_socket_body
static_main_body
flex_gripper_edge_body
dynamic_ball_body
dynamic_main_body
claw_clone_body

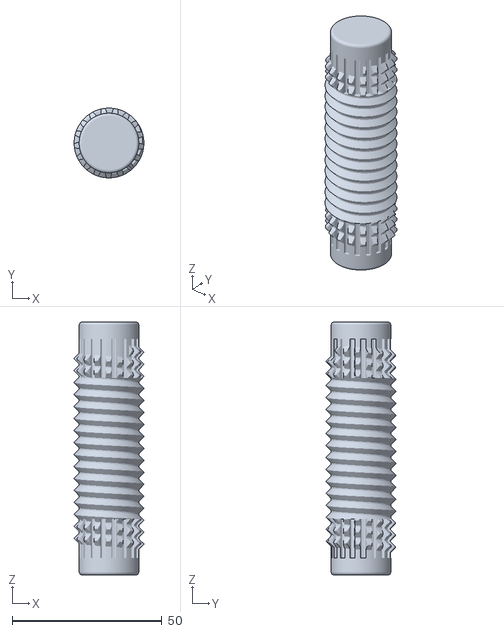
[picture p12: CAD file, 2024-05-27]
models/stl/planet.stl
23.3 x 23.3 x 84.4

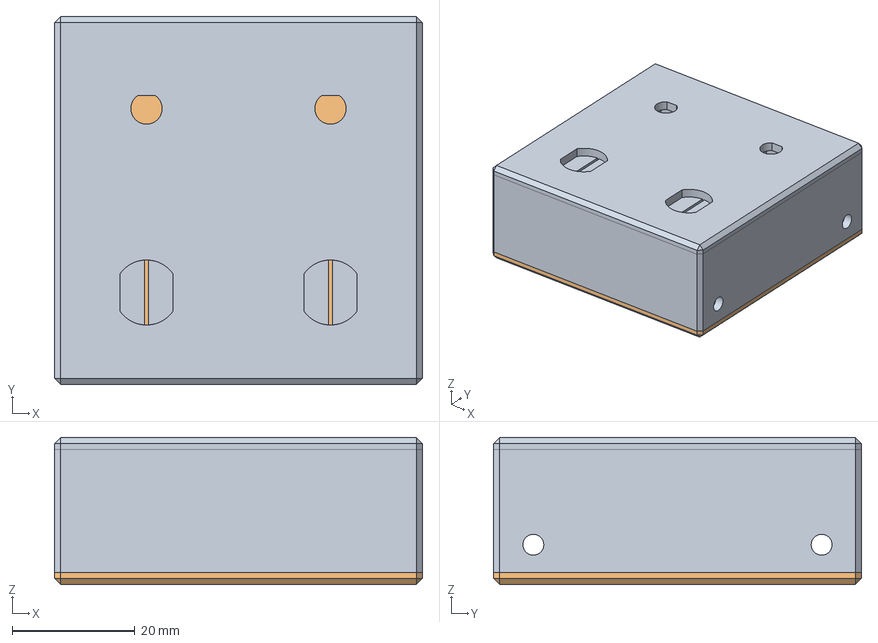
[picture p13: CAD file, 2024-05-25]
models/controller.FCStd
60.0 x 60.0 x 24.0 mm
controller_body
cover_body

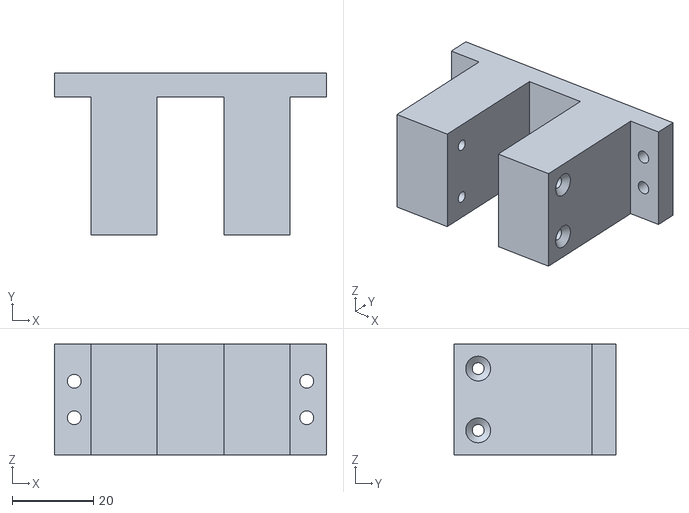
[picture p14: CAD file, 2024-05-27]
models/stl/cap.stl
67.0 x 40.0 x 27.2

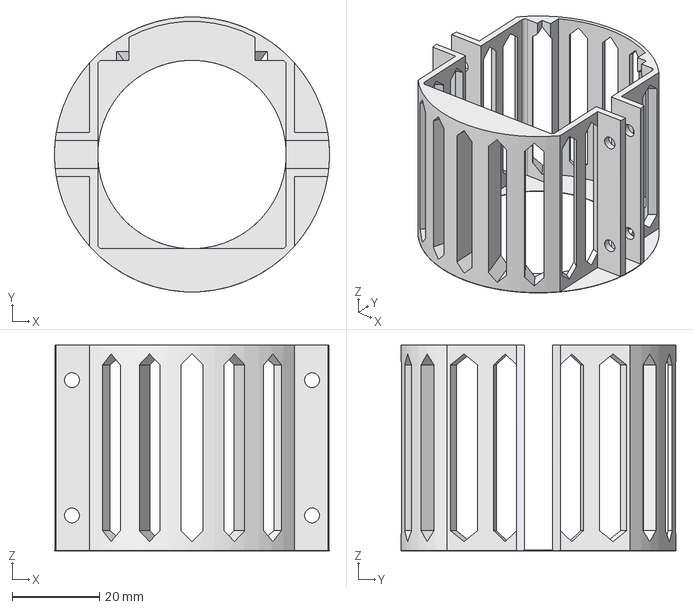
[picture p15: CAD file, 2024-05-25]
models/stepper_holder.FCStd
63.0 x 63.0 x 47.1 mm

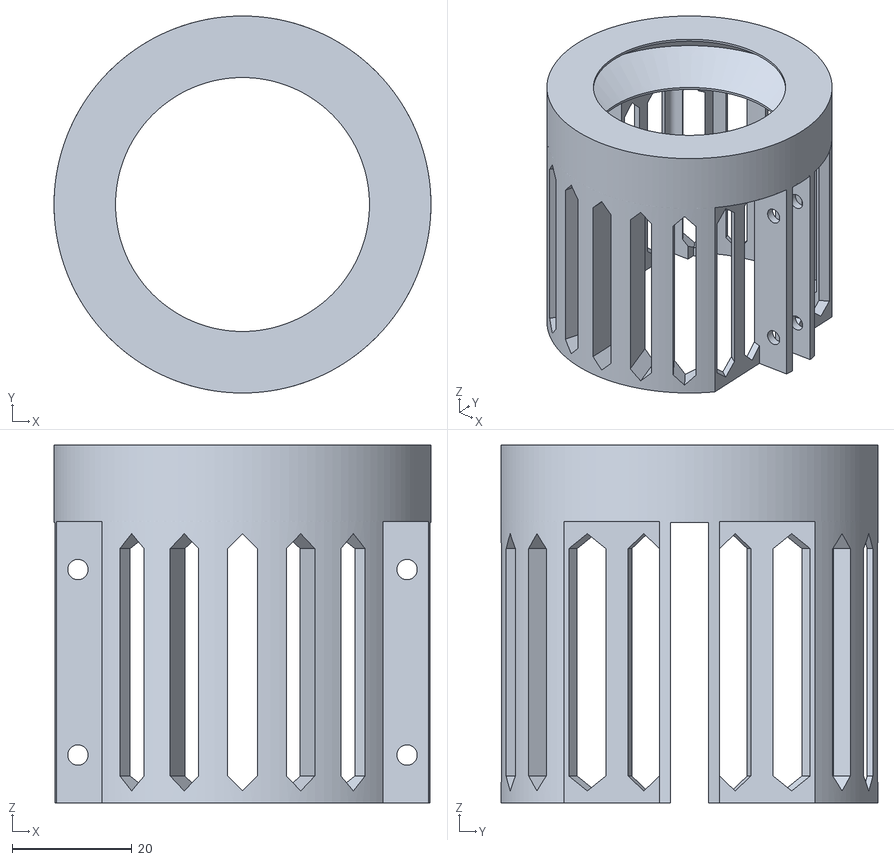
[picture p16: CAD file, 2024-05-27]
models/stl/bearing_holder_combo.stl
63.0 x 63.0 x 59.8

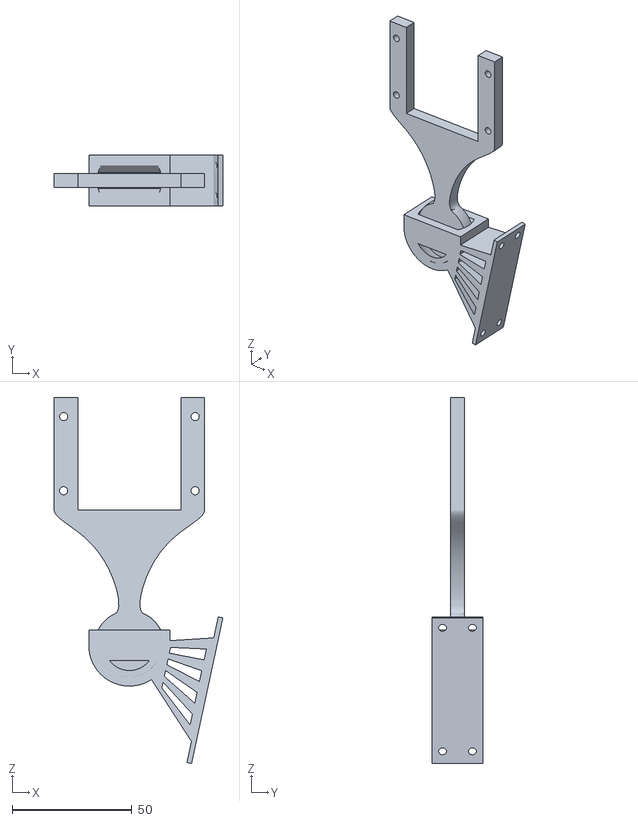
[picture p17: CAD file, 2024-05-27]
models/stl/tendon_stepper_end.stl
70.6 x 21.5 x 153.1

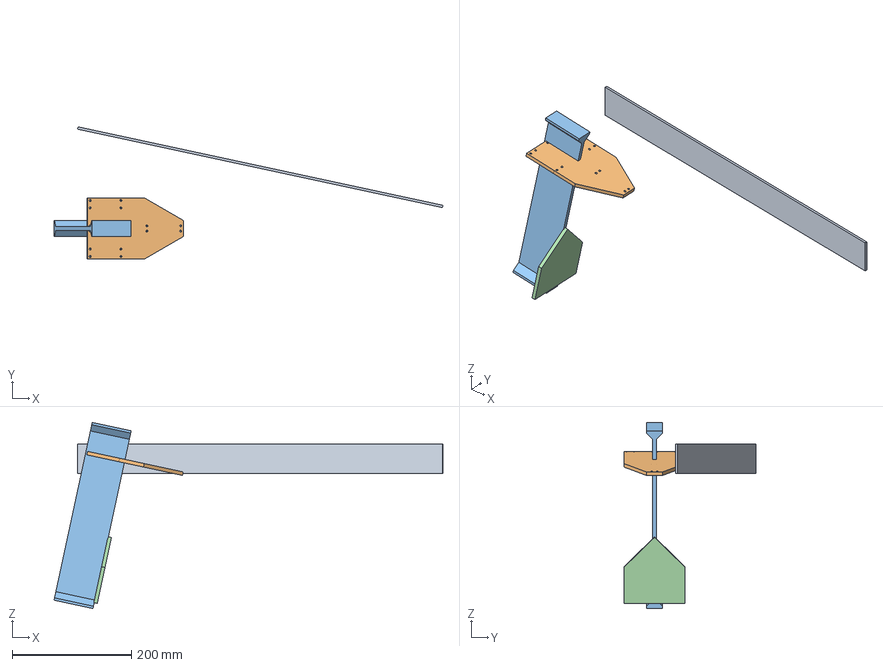
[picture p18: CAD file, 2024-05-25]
models/skeleton.FCStd
653.4 x 222.3 x 312.7 mm
arm_insertion_body
arm_swivel_plate_body
arm_origin_bone_body
arm_origin_back_plate_body

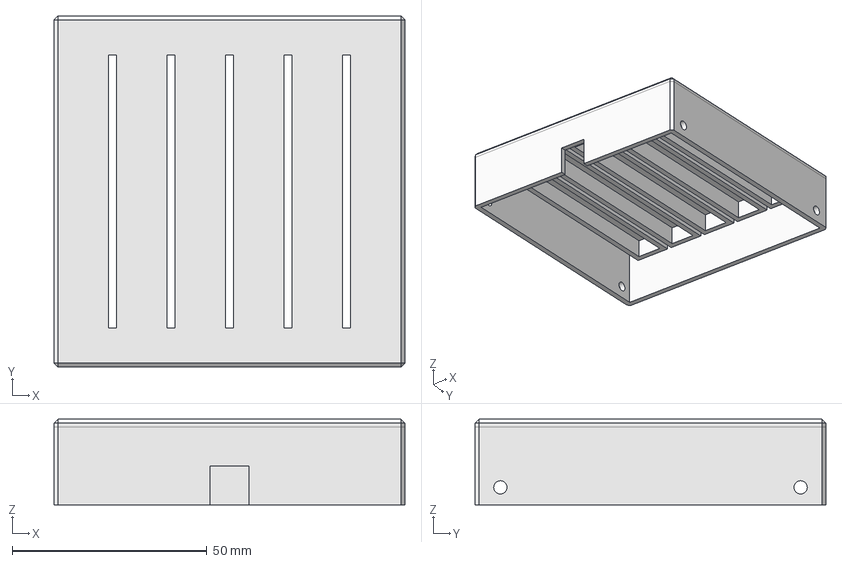
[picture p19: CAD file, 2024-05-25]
models/slider_control_box.FCStd
90.0 x 90.0 x 22.0 mm

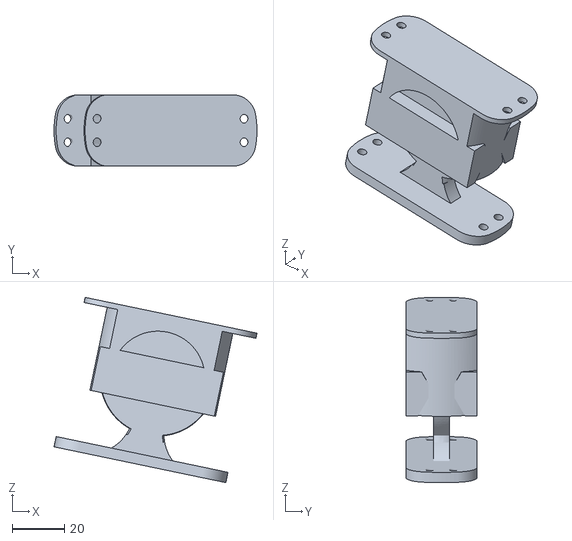
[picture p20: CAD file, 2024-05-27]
models/stl/skeleton_joint.stl
77.5 x 27.2 x 70.7

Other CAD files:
models/muscle_motor_assembly.FCStd
models/far_tendon.FCStd
models/stl/slider_bottom.stl
models/stl/slider_top.stl
models/bearing.FCStd
models/carrier.FCStd
models/circlip.FCStd
models/gear_tooth.FCStd
models/nut.FCStd
models/params.FCStd
models/planetary.FCStd
models/rod.FCStd
models/rod_extension.FCStd
models/skeleton_ball_joint.FCStd
models/stepper.FCStd
models/stl/bearing_core_screw.stl
models/stl/bearing_core_stepper.stl
models/stl/bearing_roller.stl
models/stl/carrier.stl
models/stl/circlip.stl
models/stl/driver_box_bottom.stl
models/stl/nut.stl
models/stl/screw.stl
models/stl/tendon_nut_end.stl
models/stl/webcam_mount.stl
models/thread.FCStd
models/virtual_screw.FCStd
models/webcam_mount.FCStd
models/wooden_stand_cap.FCStd

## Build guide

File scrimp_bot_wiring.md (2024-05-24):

## Scrimpt bot wiring

This is the wiring diagram for scrimp bot hardware. There are five stepper motors (2 sets of 2 muscle motor modules for arms and one for the claw), each with a linear potentiometer for control.

```mermaid
graph LR
    Laptop -- "SSH" --> Script

    subgraph "24v-34v power supply"
        PowerSupply[Vmot Power]
        PowerGnd[Vmot Ground]
    end

    subgraph SERVER
        subgraph Peripherals
            USBArduino
            USBCamera1[USB Camera 1]
            USBCamera2[USB Camera 2]
            USBCamera3[USB Camera 3]
        end

        LLM[Transformer Model]
            subgraph Script [Python Script]
                Input[Accept phrase]
                Photos[Take photos]
                Model[Send to model]
                Wire[Transmit to Arduino]
                Stop[Model self terminates]
                Input --> Photos --> Model --> Wire --> Photos
                Wire --> Stop
            end
    end

    subgraph DIVERBOX[Driver Box]
        subgraph ARDUINO
        ArduinoDigital[Arduino digital]
        ArduinoAnalog[Arduino analog]
        ArduinoGnd[Arduino ground]
        ArduinoPower[Arduino 5v]
        end

        subgraph DRIVERS
        Driver1[TMC2208 Stepper Motor Driver 1]
        Driver2[TMC2208 Stepper Motor Driver 2]
        end

        IOPower[IO 5v]
        IOGnd[IO Ground]

        MotorPower
        MotorGnd
        Cap[100uF Capacitor]
    end

    subgraph CONTROLLER[Manual Drive Controller]
        subgraph POTENTIOMETERS[Variable voltage dividers]
        Pot1[Linear pot + 10kOhm 1]
        Pot2[Linear pot + 10kOhm 2]
        end
        ControllerPower
        ControllerGND
    end

    EStop[e-stop]

    subgraph MOTORS
    StepperMotor1[Stepper Motor 1]
    StepperMotor2[Stepper Motor 2]
    end

    USBArduino -- "USB Tx/Rx on D0/D1" --> ArduinoDigital
    ArduinoGnd --> IOGnd
    ArduinoPower --> IOPower
    IOGnd --> Driver1
    IOGnd --> Driver2
    IOGnd --> ControllerGND
    ControllerGND --> Pot1
    ControllerGND --> Pot2
    ArduinoDigital -- "STEP" --> Driver1
    ArduinoDigital -- "STEP" --> Driver2
    ArduinoDigital -- "DIR" --> Driver1
    ArduinoDigital -- "DIR" --> Driver2
    IOPower --> Driver1
    IOPower --> Driver2
    IOPower --> ControllerPower
    ControllerPower --> Pot1
    ControllerPower --> Pot2
    ArduinoAnalog --> Pot1
    ArduinoAnalog --> Pot2

    MotorPower --> Cap
    Cap --> MotorGnd
    PowerGnd --> MotorGnd
    PowerSupply --> EStop
    EStop --> MotorPower
    MotorPower --> Driver1
    MotorPower --> Driver2

    MotorGnd --> Driver1
    MotorGnd --> Driver2
    Driver1 -- "Motor Connections (1A, 1B, 2A, 2B)" --> StepperMotor1
    Driver2 -- "Motor Connections (1A, 1B, 2A, 2B)" --> StepperMotor2

```

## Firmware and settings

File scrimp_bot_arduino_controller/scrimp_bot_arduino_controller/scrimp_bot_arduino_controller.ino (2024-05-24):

#include <AccelStepper.h>

// Initialize the stepper library. Specify two digital pins per driver.
AccelStepper stepperRightlower(AccelStepper::DRIVER, 3, 2); // step, direction
AccelStepper stepperLeftUpper(AccelStepper::DRIVER, 5, 4);
AccelStepper stepperLeftLower(AccelStepper::DRIVER, 7, 6);
AccelStepper stepperClaw(AccelStepper::DRIVER, 9, 8);
AccelStepper stepperRightUpper(AccelStepper::DRIVER, 11, 10);

// Stepper properties
const float DRIVER_MICROSTEPPING = 0.5; // E.g., 1/2 = 0.5
const int STEPS_PER_REVOLUTION = 200 / DRIVER_MICROSTEPPING;

const int MAX_REVS_PER_SECOND = 3;
const int MAX_STEPS_PER_SECOND = STEPS_PER_REVOLUTION * MAX_REVS_PER_SECOND;

// Slider potentiometers
const int MIN_SLIDER = 710;
const int MAX_SLIDER = 1023;
const int MID_SLIDER = 830;
const int STOP_ZONE = 90;

// REVERSE flags. Useful if motors are wired differently.
const bool REVERSE_RightLower = false;
const bool REVERSE_LeftLower = true;
const bool REVERSE_LeftUpper = false;
const bool REVERSE_RightUpper = true;
const bool REVERSE_Claw = true;

// Which analog pin is used for potentiometers.
const int ANALOG_RightLower = 2;
const int ANALOG_LeftLower = 1;
const int ANALOG_LeftUpper = 3;
const int ANALOG_RightUpper = 4;
const int ANALOG_Claw = 5;


void setup() {
  for (int i = 0; i < 5; i++) {
      initStepper(i);
  }
  Serial.begin(9600);
}

void loop() {
  // Read analog values and calculate motions

  for (int i = 0; i < 5; i++) {
    // Get the analog pin for the current stepper
    int analogPin = AnalogPinFromIndex(i);
    // Pins A1-A5 are used.
    int sliderValue = analogRead(analogPin);
    float velocity = sliderToVelocity(sliderValue);
    setStepperVelocity(i, velocity);
    runStepper(i, velocity);
  }
}

// Function to convert analog read of slider voltage divider to velocity of motor
float sliderToVelocity(int sliderValue) {
  // Constrain sliderValue within the MIN_SLIDER and MAX_SLIDER bounds
  sliderValue = constrain(sliderValue, MIN_SLIDER, MAX_SLIDER);

  if (sliderValue > MID_SLIDER + STOP_ZONE) {
    // Mapping from just above the stop zone to the max slider value, from 0 to 3.0
    return map(sliderValue, MID_SLIDER + STOP_ZONE + 1, MAX_SLIDER, 0, MAX_REVS_PER_SECOND * 100) / 100.0;
  } else if (sliderValue < MID_SLIDER - STOP_ZONE) {
    // Mapping from the min slider value to just below the stop zone, from -3.0 to 0
    return map(sliderValue, MIN_SLIDER, MID_SLIDER - STOP_ZONE - 1, -MAX_REVS_PER_SECOND * 100, 0) / 100.0;
  } else {
    return 0; // Stop zone
  }
}

// Function to return a pointer to the corresponding stepper based on the index
AccelStepper* stepperFromIndex(int index) {
  switch (index) {
    case 0: return &stepperRightlower;
    case 1: return &stepperLeftLower;
    case 2: return &stepperLeftUpper;
    case 3: return &stepperRightUpper;
    case 4: return &stepperClaw;
    default: return nullptr; // Return null if the index is out of bounds
  }
}

// Function to return the REVERSE flag for the corresponding stepper based on the index
bool ReverseFromIndex(int index) {
  switch (index) {
    case 0: return REVERSE_RightLower;
    case 1: return REVERSE_LeftLower;
    case 2: return REVERSE_LeftUpper;
    case 3: return REVERSE_RightUpper;
    case 4: return REVERSE_Claw;
    default: return true; // Default to true if the index is out of bounds
  }
}

// Function to return the analog pin for the corresponding stepper based on the index
int AnalogPinFromIndex(int index) {
  switch (index) {
    case 0: return ANALOG_RightLower;
    case 1: return ANALOG_LeftLower;
    case 2: return ANALOG_LeftUpper;
    case 3: return ANALOG_RightUpper;
    case 4: return ANALOG_Claw;
    default: return -1; // Default if the index is out of bounds
  }
}

// Set up steppers
void initStepper(int index) {
  AccelStepper* stepper = stepperFromIndex(index);
  if (!stepper) return;
  // Set the maximum speed in steps per second:
  stepper->setMaxSpeed(MAX_STEPS_PER_SECOND);
}

// Move a stepper at some velocity
void setStepperVelocity(int stepperIndex, float motorRevsPerSec) {
  AccelStepper* stepper = stepperFromIndex(stepperIndex);
  if (!stepper) return;
  bool REVERSE = ReverseFromIndex(stepperIndex);
  if (!REVERSE) {
    motorRevsPerSec = -motorRevsPerSec;
  }
  float stepsPerSecond = motorRevsPerSec * STEPS_PER_REVOLUTION;
  stepper->setSpeed(stepsPerSecond);
}

// Move a stepper 
void runStepper(int index, float velocity) {
  AccelStepper* stepper = stepperFromIndex(index);
  if (!stepper) return;
  if (velocity == 0) {
    stepper->disableOutputs(); // Disable holding current
  } else {
    stepper->enableOutputs(); // Enable outputs if there is a velocity
    stepper->runSpeed();
  }
}

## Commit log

2024-05-24 add wiring diagram
2024-05-24 add arduino script
2024-05-24 fix stepper controller directions
    [scrimp_bot_arduino_controller.ino]
2024-05-24 disable current when motor static
2024-05-25 add models
    [bearing.FCStd, carrier.FCStd, circlip.FCStd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]
2024-05-27 add stl files
    [bearing_core_screw.stl, bearing_core_stepper.stl, bearing_holder_combo.stl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]
